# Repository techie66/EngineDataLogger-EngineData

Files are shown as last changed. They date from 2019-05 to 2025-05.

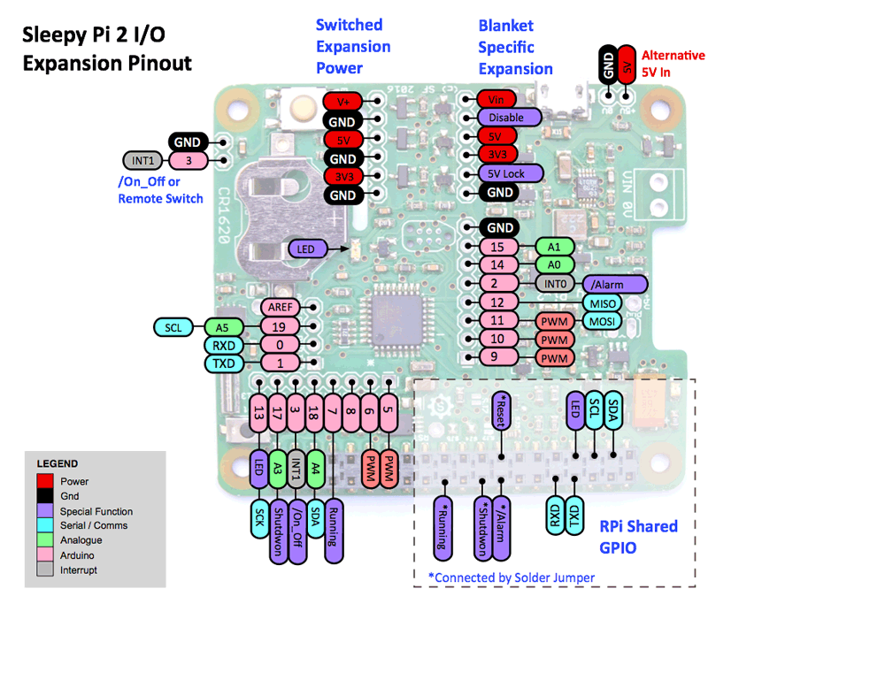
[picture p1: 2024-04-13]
hardware/Sleepy-Pi-2-Expansion-Annotated-2-1000.png

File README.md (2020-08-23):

# Engine Data Logger - Engine Data
This project has been developed using Automake and Makefile setup from: https://github.com/sudar/Arduino-Makefile

Sleepy Pi 2 needs to have software power jumper enabled if programming from the Pi.
	i2cset -y 1 0x24 0xFD
Turn it off with:
	i2cset -y 1 0x24 0xFF

It's not strictly necessary, but Arduino-Makefile includes a script to reset the Arduino. It would need to be setup to set pin 22 of the RPi's GPIO high for about 1/3 of a second. Alternatively, https://github.com/SpellFoundry/avrdude-rpi provides a patched avrdude that handles this for you. This is the approach I have setup here. The Makefile points to a special avr_tools directory that contains this patched version. None of this is necessary if you are willing to manually hit the reset button whenever you try to upload code.

## Componenents
- [EngineDataLogger(EDL)](https://github.com/techie66/EngineDataLogger)
- [EDL - Dashboard](https://github.com/techie66/EngineDataLogger---Dashboard)
- [EDL - Front Controls](https://github.com/techie66/EngineDataLogger-FrontControls)
- ->[EDL - EngineData](https://github.com/techie66/EngineDataLogger-EngineData)

# License
EngineDataLogger is licensed under the GNU GPLv2. Dependencies are licensed under their respective licenses. See LICENSE for full text of GPLv2.

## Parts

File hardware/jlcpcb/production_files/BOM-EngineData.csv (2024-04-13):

Comment | Designator | Footprint | LCSC
15V standoff | D1,D4 | D_SMB | C113989
1k | R23,R24,R6,R7,R9 | R_0402_1005Metric | C11702
100nf | C1,C13,C14,C2,C3,C4,Cboot1 | C_0402_1005Metric | C1525
MCP2515-xSO | U12,U5 | SOIC-18W_7.5x11.6mm_P1.27mm | C153782
33pf | C15,C16,C5,C6 | C_0402_1005Metric | C1562
TCA9517DR | U8 | SOIC-8_L4.9-W3.9-P1.27-LS6.0-BL | C182421
EL817 | U2,U9 | EasyEDA-C183799-smd-SOP-4_L6.5-W4.6-P2.54-LS10.2-TL | C183799
120R | R11,R16 | R_0402_1005Metric | C25079
470 | R5 | R_0402_1005Metric | C25117
100k | R12,R13,R17,R18,Rfbt1 | R_0402_1005Metric | C25741
10k | R10,R8 | R_0603_1608Metric | C25804
24K9 1% | Rfbb1 | R_0402_1005Metric | C25874
1 uF | C9 | C_0805_2012Metric | C28323
8uH, 14m | L1 | L_Bourns_SRP7028A_7.3x6.6mm | C408450
2k | R19,R2,R20,R3,R4 | R_0402_1005Metric | C4109
2.2k | R1 | R_0603_1608Metric | C4190
10uf | Cin1 | C_0805_2012Metric | C440198
22uF | Cout1,Cout2,Cout3,Cout4 | C_0805_2012Metric | C45783
30pf | C17,C18 | C_0402_1005Metric | C5182450
220nf | Chf1 | C_0805_2012Metric | C5378
14.7456 Mhz | Y3 | Crystal_SMD_3225-4Pin_3.2x2.5mm | C557186
SC16IS752IPW | U14 | TSSOP-28_4.4x9.7mm_P0.65mm | C57156
TXB0104PW | U13,U3 | TSSOP-14_4.4x5mm_P0.65mm | C60708
TJA1051T | U11,U4 | SOIC-8_3.9x4.9mm_P1.27mm | C6952
LMR33630ADDA | U7 | Texas_HSOP-8-1EP_3.9x4.9mm_P1.27mm_ThermalVias | C841384
12Mhz | Y1,Y2 | Crystal_SMD_3225-4Pin_3.2x2.5mm | C9002
Jumper_NO_Small | JP1 | SolderJumper-2_P1.3mm_Open_RoundedPad1.0x1.5mm
Jumper_NO_Small | JP2 | SolderJumper-2_P1.3mm_Open_RoundedPad1.0x1.5mm

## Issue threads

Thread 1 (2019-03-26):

"programming mode"

techie66, 2019-03-26:
enable a "programming mode" that lets a controlling I2C master set conversion factors.
-Store them in flash
-I2C read/write
-Separate values for each variable in conversion factor (wheel diameter, pulses per rotation, etc...)

techie66, 2020-02-27:
eb993df9de465faafcb15cc0d58ad687136bdcc4 added the functions that enable this. Just have to define an interface to actually do it.

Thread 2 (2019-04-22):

Odometer

techie66, 2019-04-22:
Project needs an odometer.
1. Basic setting should be tire diameter
2. EEPROM storage
3. Only write to eeprom on power off.
4. Rotate storage area.

techie66, 2019-04-22:
#1 Programming mode should enable setting diameter

techie66, 2019-04-23:
I've got a local commit that does 1 and 2 from above.  EEPROM is read during setup and globals are set and updated via the wheel ISR.
Just need to handle writing data back to EEPROM which should take care of 3 and 4.

techie66, 2020-02-27:
This is all taken care of by eb993df9de465faafcb15cc0d58ad687136bdcc4

Closed 2020-02-27.

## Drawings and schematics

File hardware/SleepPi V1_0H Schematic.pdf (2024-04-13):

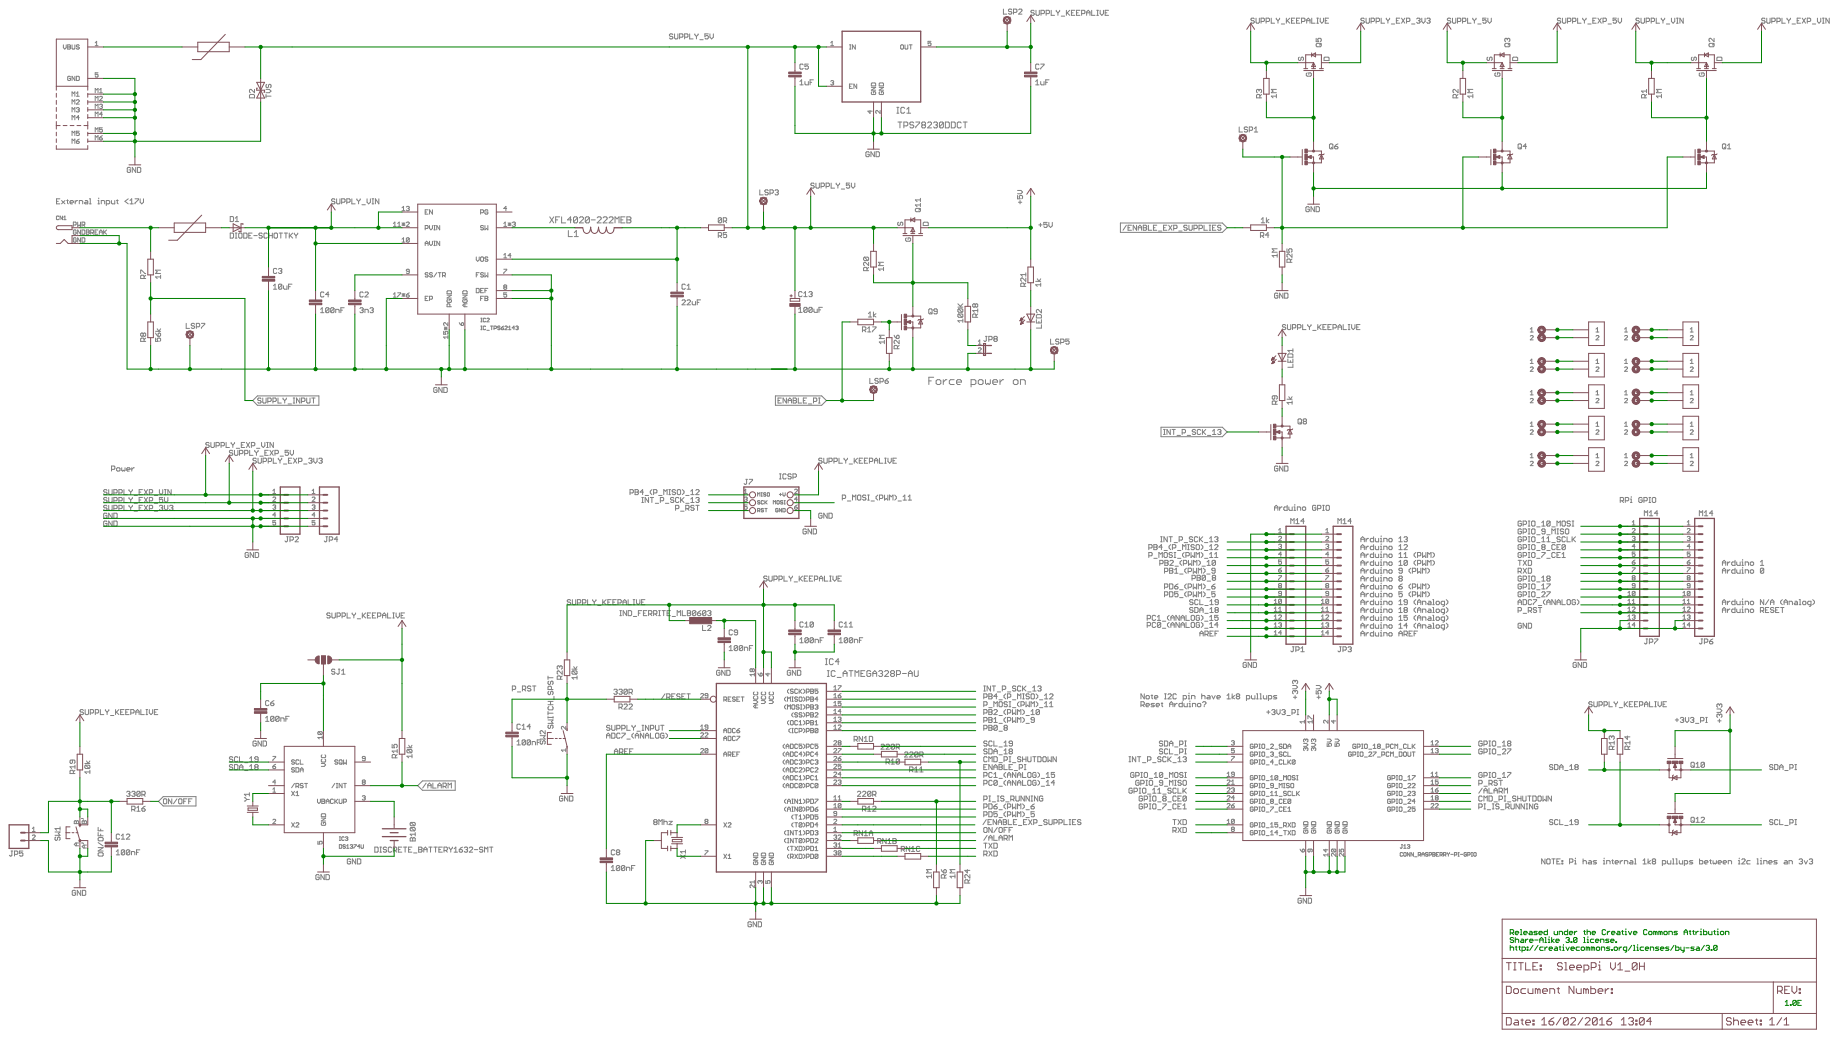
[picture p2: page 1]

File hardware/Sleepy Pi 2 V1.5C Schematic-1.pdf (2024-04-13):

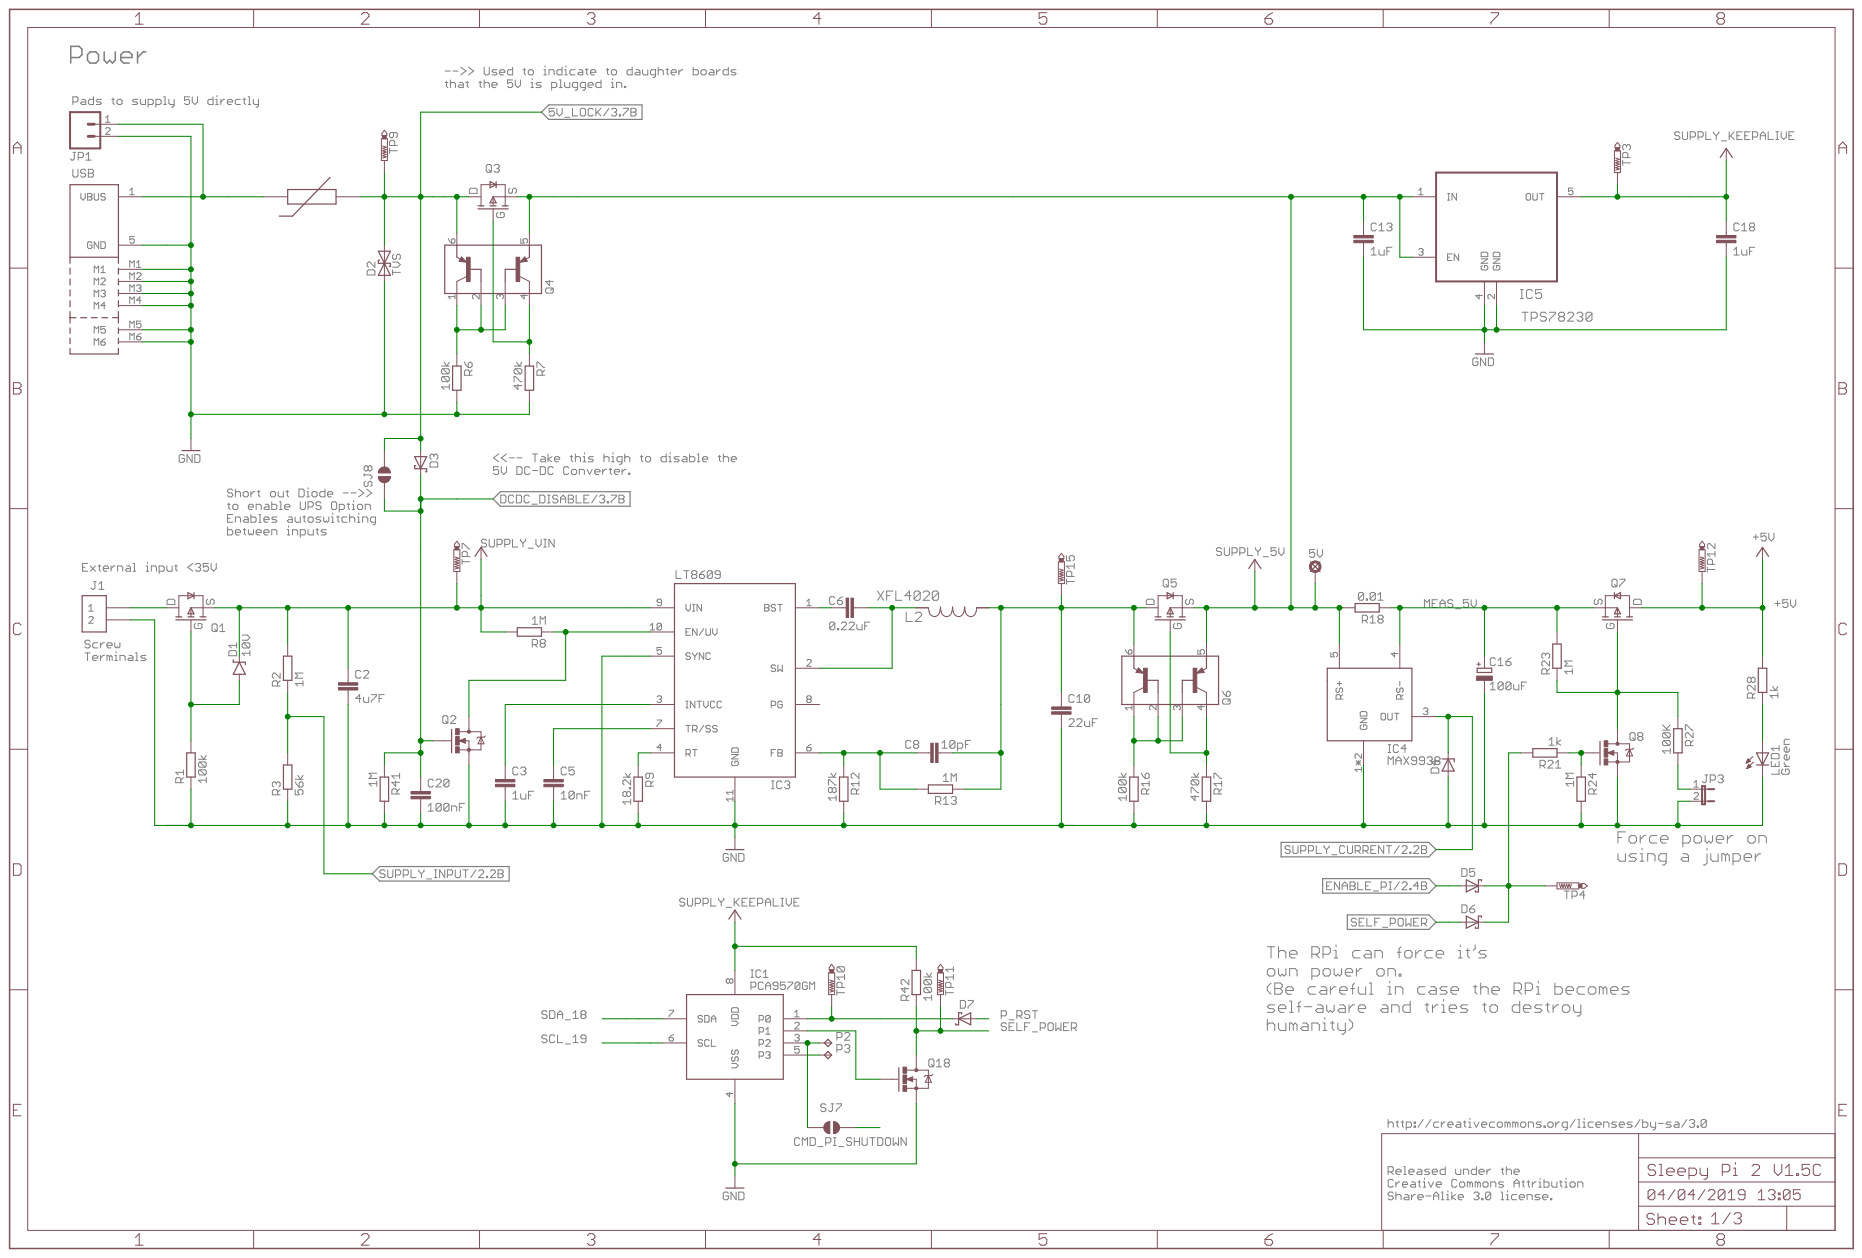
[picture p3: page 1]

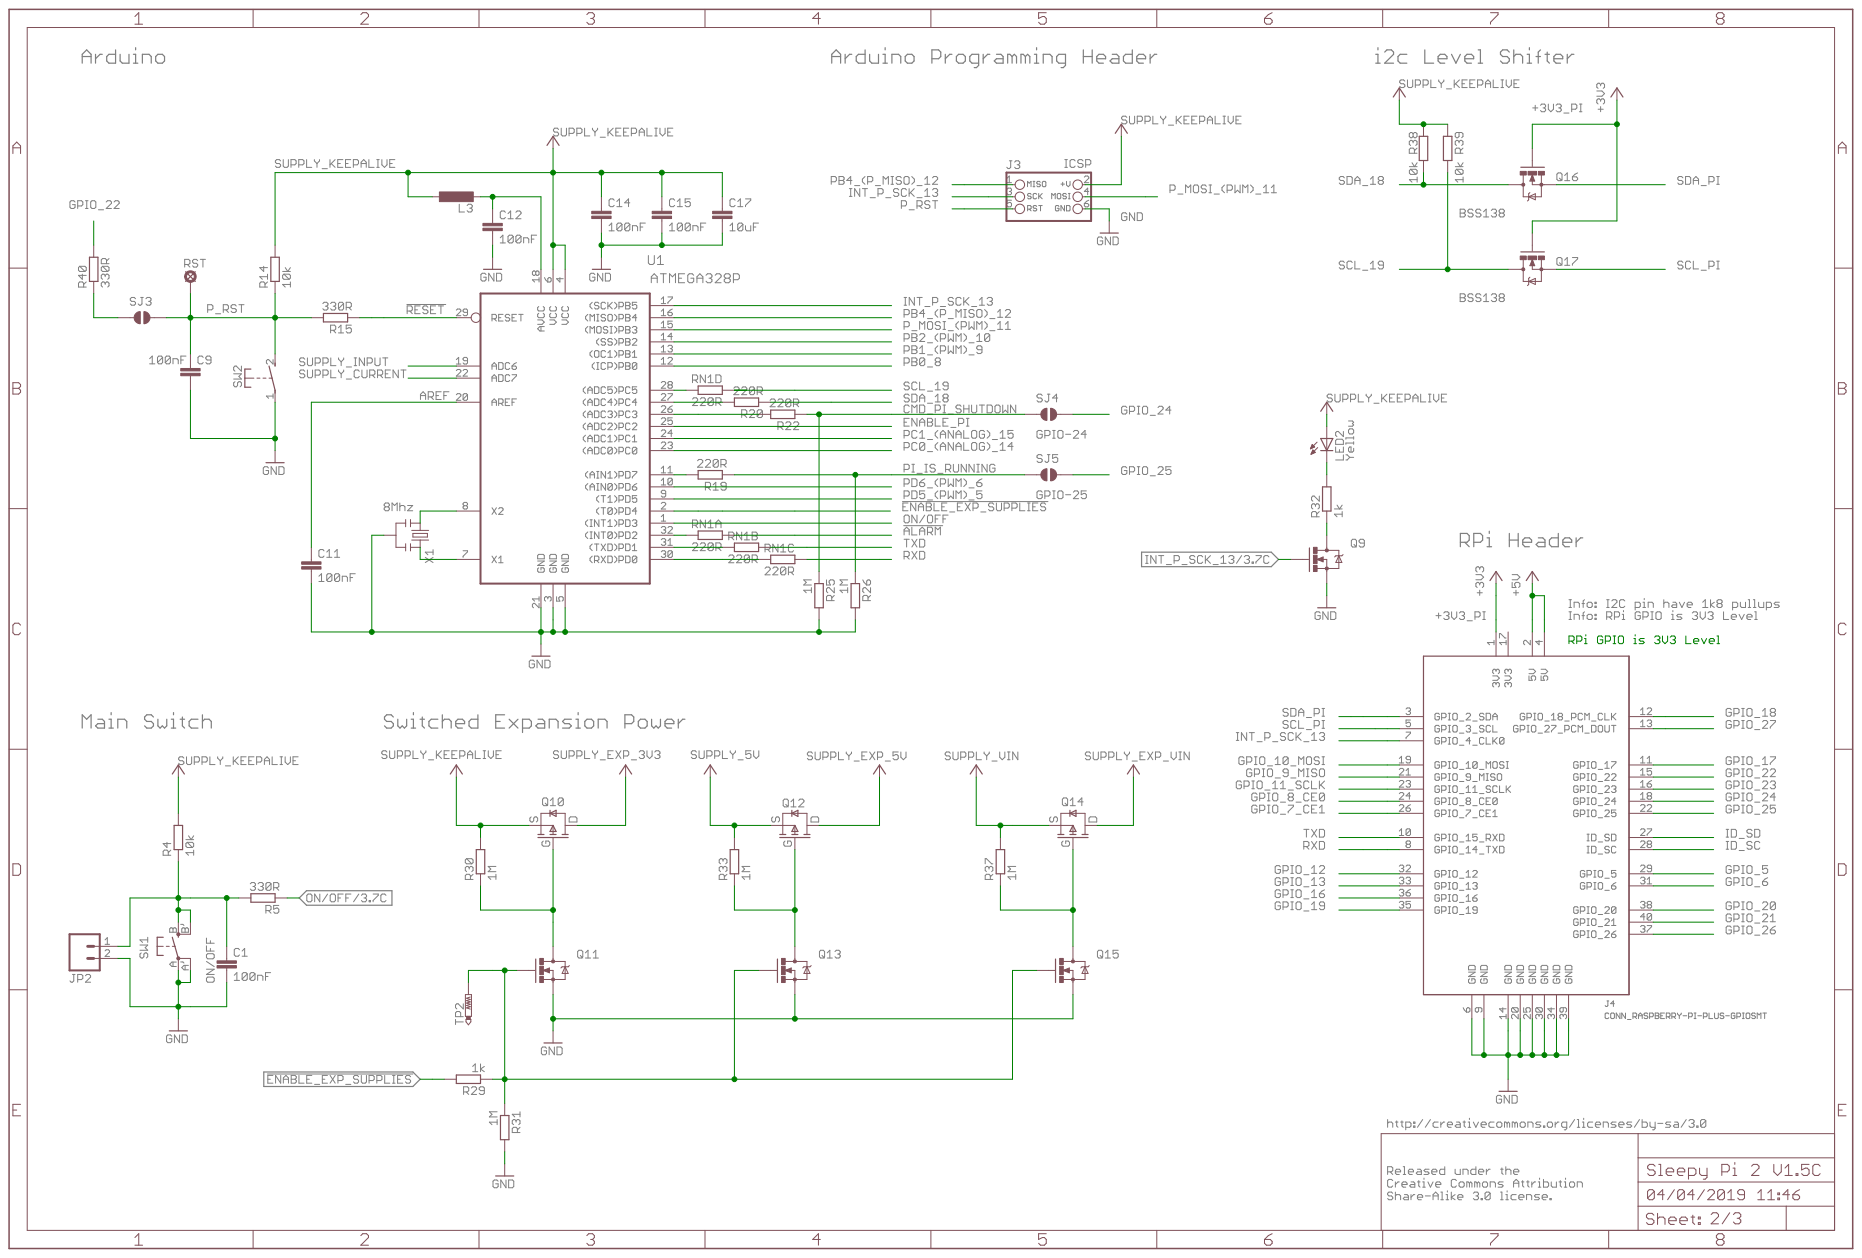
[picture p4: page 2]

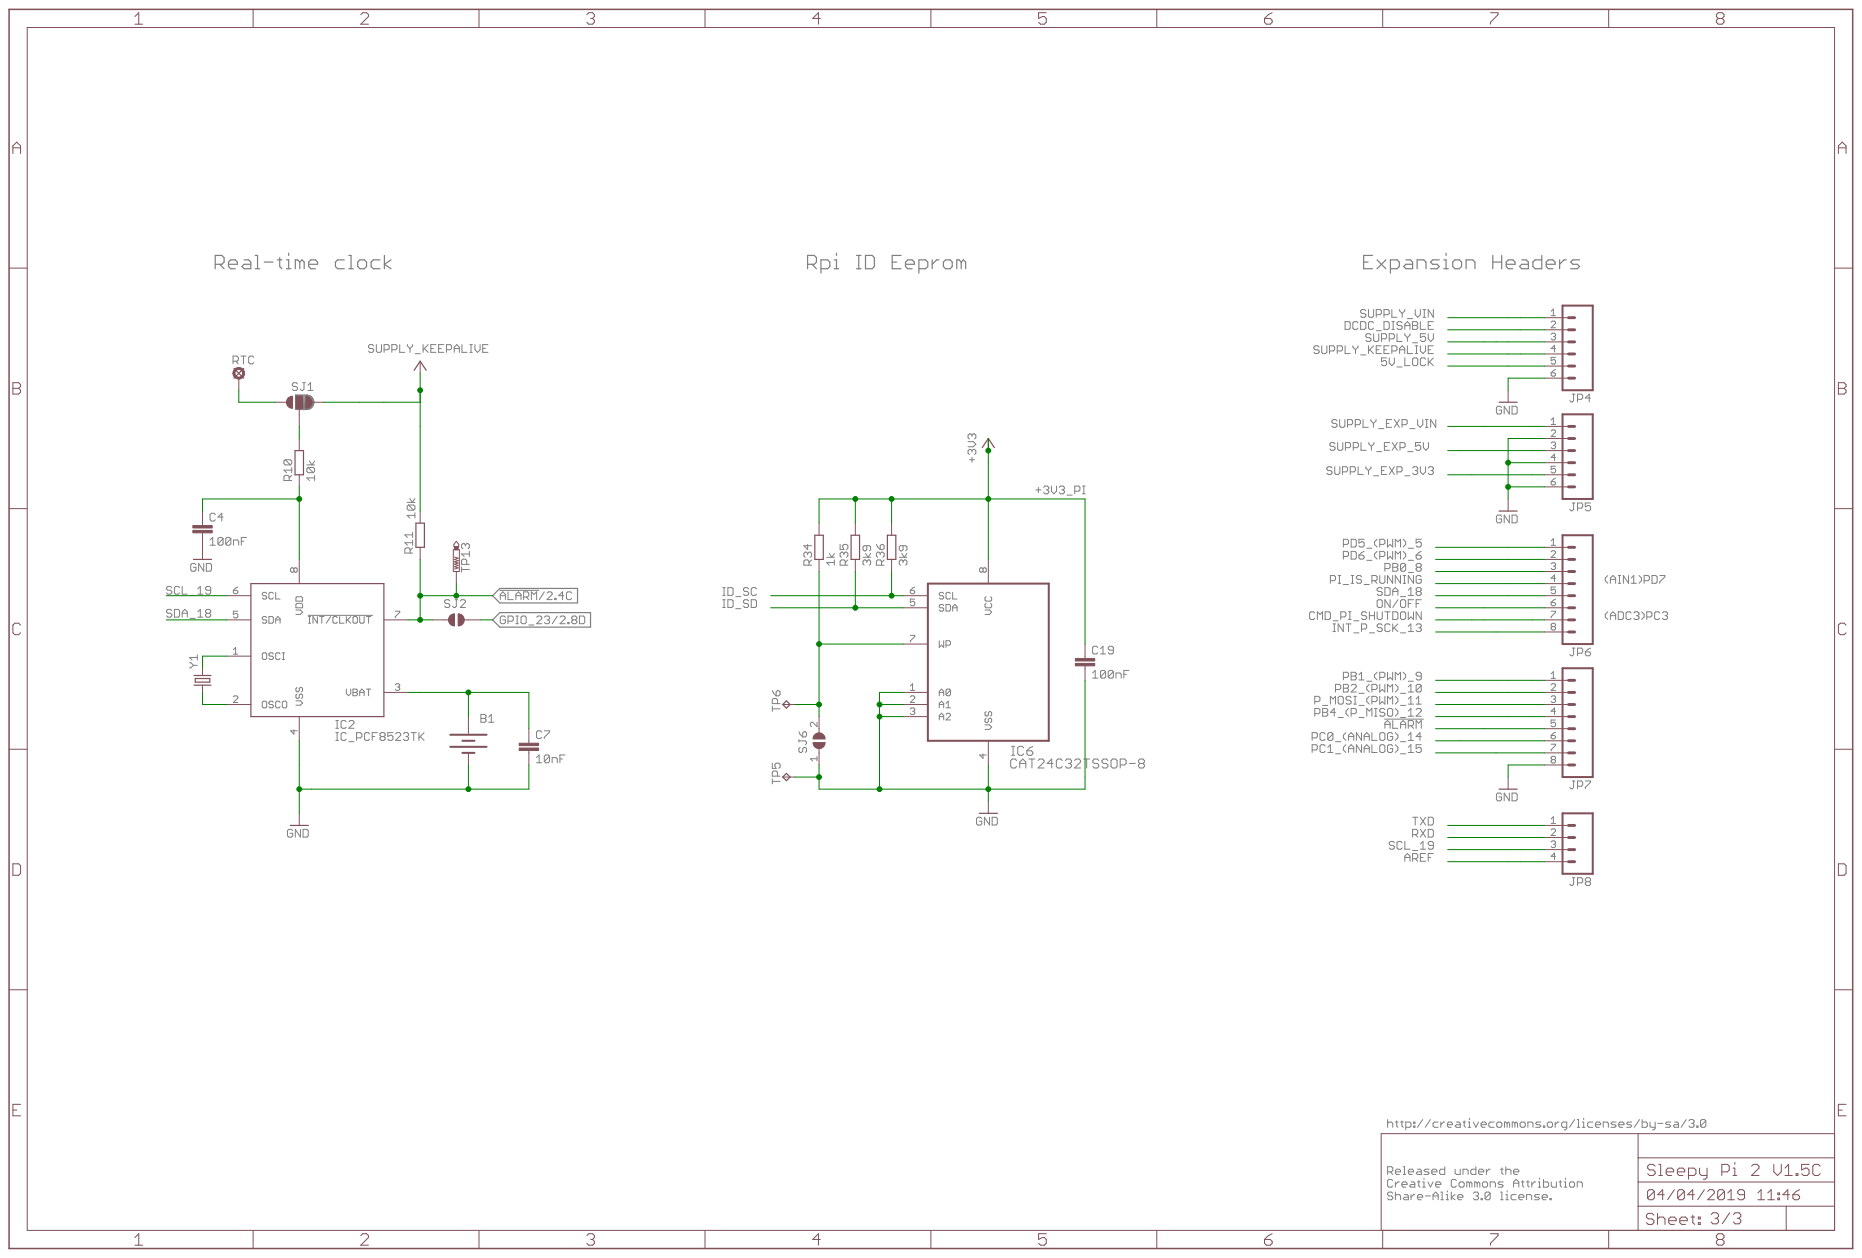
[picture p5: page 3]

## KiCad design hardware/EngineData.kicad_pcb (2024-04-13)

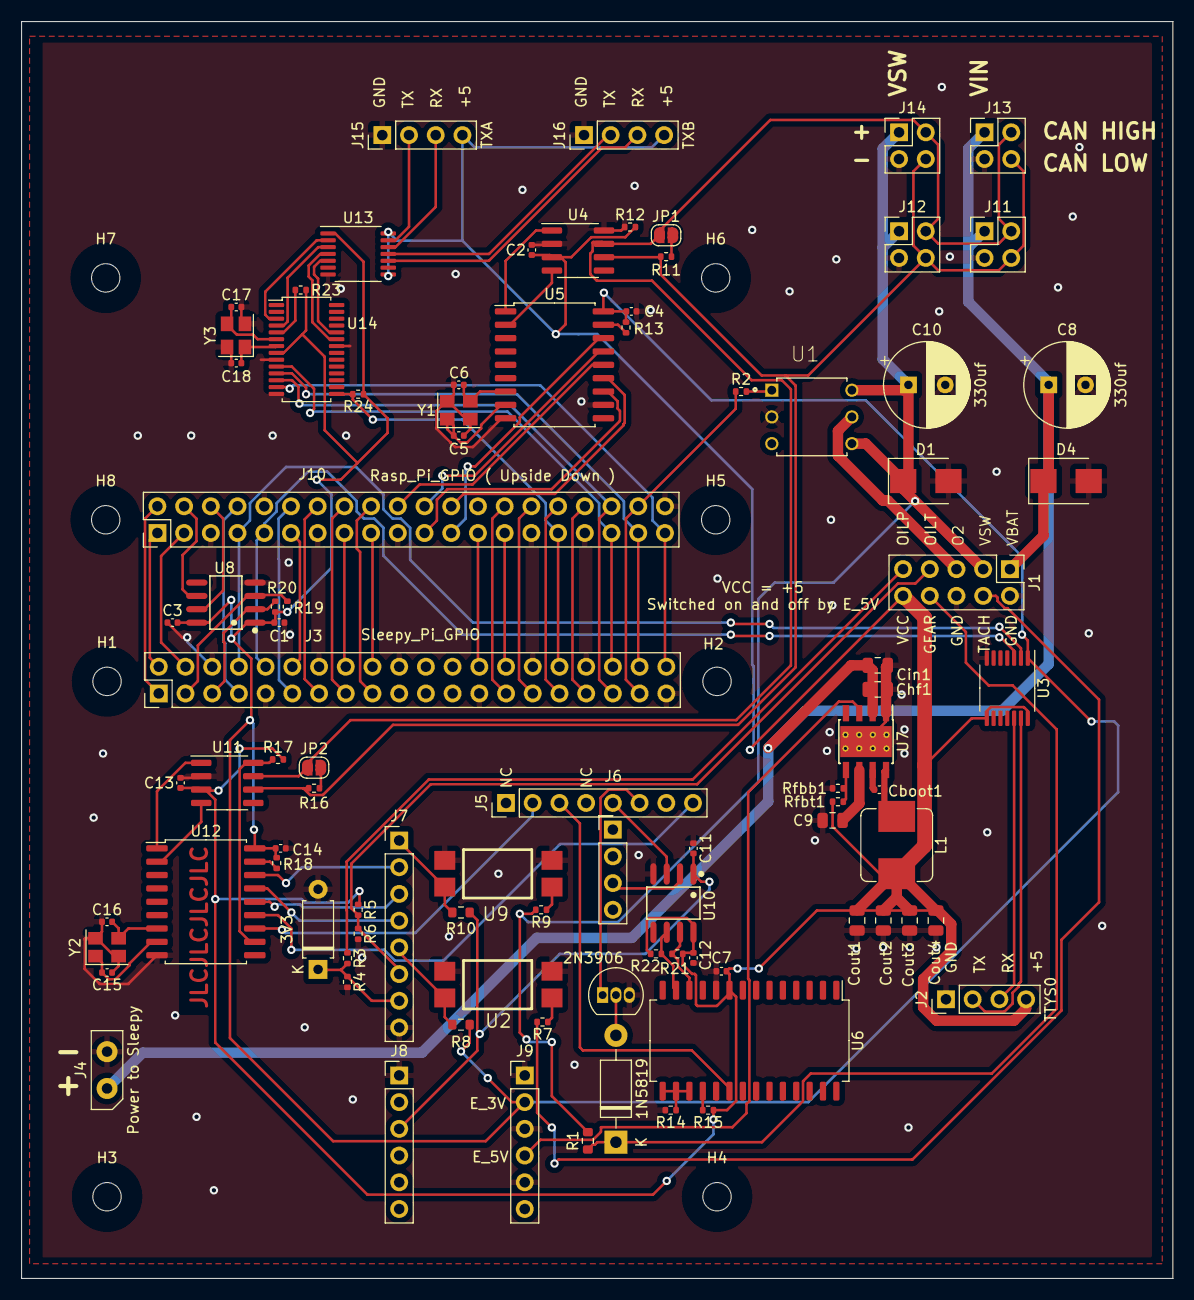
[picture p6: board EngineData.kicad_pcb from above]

Board: 2 copper layers, 109.5 x 119.5 mm, 100 parts (0 on the bottom side), 98 nets.

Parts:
C1, C2, C3, C4, C7, C11, C12, C13, C14: 100nf; C_0402_1005Metric
C5, C6, C15, C16: 33pf; C_0402_1005Metric
C8, C10: 330uf; CP_Radial_D8.0mm_P3.50mm
C9: 1 uF; C_0805_2012Metric
C17, C18: 30pf; C_0402_1005Metric
Cboot1: 100nf; C_0402_1005Metric
Chf1: 220nf; C_0805_2012Metric
Cin1: 10uf; C_0805_2012Metric
Cout1, Cout2, Cout3, Cout4: 22uF; C_0805_2012Metric
D1, D4: 15V standoff; D_SMB
D2: 1N5819; D_DO-41_SOD81_P10.16mm_Horizontal
D3: 3V3; D_A-405_P7.62mm_Horizontal
H1, H2, H3, H4, H5, H6, H7, H8: MountingHole; MountingHole_2.7mm_M2.5
J1: External Connector; PinHeader_2x05_P2.54mm_Vertical
J2: TTYS0; PinHeader_1x04_P2.54mm_Vertical
J3: Sleepy_Pi_GPIO; PinHeader_2x20_P2.54mm_Vertical
J4: Power to Sleepy; S_Pi_PWR
J5, J7: Conn_01x08; PinHeader_1x08_P2.54mm_Vertical
J6: Conn_01x04; PinHeader_1x04_P2.54mm_Vertical
J8, J9: Conn_01x06; PinHeader_1x06_P2.54mm_Vertical
J10: Rasp_Pi_GPIO ( Upside Down ); PinHeader_2x20_P2.54mm_Vertical
J11, J12, J13, J14: 2x2; PinHeader_2x02_P2.54mm_Vertical
J15: TXA; PinHeader_1x04_P2.54mm_Vertical
J16: TXB; PinHeader_1x04_P2.54mm_Vertical
JP1, JP2: Jumper_NO_Small; SolderJumper-2_P1.3mm_Open_RoundedPad1.0x1.5mm
L1: 8uH, 14m; L_Bourns_SRP7028A_7.3x6.6mm
Q1: 2N3906; TO-92_Inline
R1: 2.2k; R_0603_1608Metric
R2, R3, R4, R19, R20: 2k; R_0402_1005Metric
R5: 470; R_0402_1005Metric
R6, R7, R9, R23, R24: 1k; R_0402_1005Metric
R8, R10: 10k; R_0603_1608Metric
R11, R16: 120R; R_0402_1005Metric
R12, R13, R15, R17, R18: 100k; R_0402_1005Metric
R14, R21, R22: 4K7 1%; R_0402_1005Metric
Rfbb1: 24K9 1%; R_0402_1005Metric
Rfbt1: 100k 1%; R_0402_1005Metric
U1: G3VM-31BR; DIP762W50P254L737H485Q6
U2, U9: EL817; EasyEDA-C183799-smd-SOP-4_L6.5-W4.6-P2.54-LS10.2-TL
U3, U13: TXB0104PW; TSSOP-14_4.4x5mm_P0.65mm
U4, U11: TJA1051T; SOIC-8_3.9x4.9mm_P1.27mm
U5, U12: MCP2515-xSO; SOIC-18W_7.5x11.6mm_P1.27mm
U6: MCP23017-E/SO; SOIC-28W_7.5x18.7mm_P1.27mm
U7: LMR33630ADDA; Texas_HSOP-8-1EP_3.9x4.9mm_P1.27mm_ThermalVias
U8, U10: TCA9517DR; SOIC-8_L4.9-W3.9-P1.27-LS6.0-BL
U14: SC16IS752IPW; TSSOP-28_4.4x9.7mm_P0.65mm
Y1, Y2: 12Mhz; Crystal_SMD_3225-4Pin_3.2x2.5mm
Y3: 14.7456 Mhz; Crystal_SMD_3225-4Pin_3.2x2.5mm

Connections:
3V3: C11.2, J8.3, R10.2, U10.1 (VCCA)
/CAN_H: J11.2, J12.2, J13.2, J14.2, JP1.1 (A), JP2.1 (A), U4.7 (CANH), U11.7 (CANH)
/CAN_L: J11.4, J12.4, J13.4, J14.4, R11.1, R16.1, U4.6 (CANL), U11.6 (CANL)
/GE1: J3.2, J10.1
/GE2: J3.4, J10.3
/GE4: J3.8, J10.7, U3.2 (A1)
/GE5: J3.10, J10.9, U3.3 (A2)
/GE6: J3.12, J10.11
/GE8: J3.16, J10.15
/GE9: J3.18, J10.17
/GE11: J10.21, U5.12 (~INT)
/GE12: J10.23, U5.16 (~CS)
/GE13: J3.26, J10.25
/GE14: J3.28, J10.27
/GE16: J3.32, J10.31, R24.2, U14.15 (~IRQ)
/GE18: J3.36, J10.35, U14.10 (A0/~CS)
/GE19: J3.38, J10.37, U14.11 (A1/SI)
/GE20: J3.40, J10.39, U14.13 (SCL/SCLK)
/GEAR: D2.1 (K), J1.8, R1.1
/GO1: J3.1, J10.2
/GO4: J3.7, J10.8
/GO6: J3.11, J10.12
/GO7: J3.13, J10.14
/GO8: J3.15, J10.16
/GO9: J3.17, J10.18
/GO10: J10.20, U5.14 (SI)
/GO11: J10.22, U5.15 (SO)
/GO12: J10.24, U5.13 (SCK)
/GO14: J3.27, J10.28
/GO15: J3.29, J10.30
/GO16: J3.31, J10.32
/GO17: J3.33, J10.34
/GO18: J3.35, J10.36, U14.12 (n.c./SO)
/GO19: J3.37, J10.38, R2.1
/IO Expander/SCL: R21.1, U6.12 (SCK), U10.7 (SCLB)
/IO Expander/SDA: R22.1, U6.13 (SDA), U10.6 (SDAB)
/MCP2515 w|trans1/EN_TX: R17.1, U11.8 (S), U12.11 (~RX0BF)
/MCP2515 w|trans1/RXCAN: U11.4 (RXD), U12.2 (RXCAN)
/MCP2515 w|trans1/TXCAN: U11.1 (TXD), U12.1 (TXCAN)
/MCP2515 w|trans/RXCAN: U4.4 (RXD), U5.2 (RXCAN)
/MCP2515 w|trans/TXCAN: U4.1 (TXD), U5.1 (TXCAN)
/O2POW: J1.5, U1.5
/OIL_P: J1.9, R3.1
/OIL_T: J1.7, J7.6, R5.2, R6.1
/PB0_8: J5.3, U6.20 (INTA)
/PB1_9: J7.1, R10.1, U9.4
/PB2_10: J7.2, U12.16 (~CS)
/PC1_A1: D3.1 (K), J7.7, R3.2, R4.1
/PD2_2: J7.5, R8.1, U2.4
/PD3_3: J5.6, Q1.1 (E)
/PD6_6: J5.2, U12.12 (~INT)
/PI_SCL: J10.6, U8.7 (SCLB)
/Pi_SDA: J10.4, U8.6 (SDAB)
/SH_SCL: J3.5, R20.2, U8.2 (SCLA)
/SH_SDA: J3.3, R19.2, U8.3 (SDAA)
/S_MISO_12: J7.4, U12.15 (SO)
/S_MOSI_11: J7.3, U12.14 (SI)
/S_SCK: J5.8, U12.13 (SCK)
/S_SCL: J6.3, U10.2 (SCLA)
/S_SDA: J5.5, U10.3 (SDAA)
/TACH: J1.4, R7.2
/UARTs/RST: R23.2, U14.5 (~RESET)
/UARTs/RXA: U13.3 (A2), U14.4 (RXA)
/UARTs/RXB: U13.5 (A4), U14.24 (RXB)
/UARTs/TXA: U13.2 (A1), U14.3 (TXA)
/UARTs/TXB: U13.4 (A3), U14.23 (TXB)
/VBAT: C8.1, Chf1.2, Cin1.2, D4.1 (A1), J1.1, J4.1, J11.1, J13.1, U7.2 (VIN)
/VSW: C10.1, D1.1 (A1), J1.3, J12.1, J14.1, R1.2, R9.2, U1.4, U1.6
E_3V3: C1.2, C3.2, C4.2, C14.2, J9.2, R8.2, R13.2, R18.2, R19.1, R20.1, R23.1, R24.1, U3.1 (VCCA), U5.18 (VDD), U8.1 (VCCA), U8.8 (VCCB), U12.18 (VDD), U13.1 (VCCA), U14.8 (VDD)
E_5V: J9.4, U7.3 (EN)
GND: C1.1, C2.2, C3.1, C4.1, C5.1, C6.1, C7.2, C8.2, C9.1, C10.2, C11.1, C12.1, C13.2, C14.1, C15.1, C16.1, C17.2, C18.1, Chf1.1, Cin1.1, Cout1.2, Cout2.2, Cout3.2, Cout4.2, D1.2 (A2), D3.2 (A), D4.2 (A2), J1.2, J1.6, J2.1, J3.6, J3.9, J3.14, J3.20, J3.25, J3.30, J3.34, J3.39, J4.2, J7.8, J8.1, J9.1, J9.3, J9.5, J10.5, J10.10, J10.13, J10.19, J10.26, J10.29, J10.33, J10.40, J11.3, J12.3, J13.3, J14.3, J15.1, J16.1, Q1.3 (C), R4.2, R6.2, R12.1, R14.2, Rfbb1.2, U1.2, U2.2, U2.3, U3.7 (GND), U4.2 (GND), U4.8 (S), U5.9 (VSS), U5.11 (~RX0BF), U6.10 (VSS), U7.1 (PGND), U7.9 (AGND), U8.4 (GND), U9.2, U9.3, U10.4 (GND), U11.2 (GND), U12.9 (VSS), U13.7 (GND), U14.9 (I2C/~SPI), U14.14 (SDA/VSS), U14.22 (VSS), Y1.2, Y1.4, Y2.2, Y2.4, Y3.2, Y3.4
unnamed: C5.2, U5.8 (OSC1), Y1.1
unnamed: C6.2, U5.7 (OSC2), Y1.3
unnamed: C9.2, U7.6 (VCC)
unnamed: C15.2, U12.8 (OSC1), Y2.1
unnamed: C16.2, U12.7 (OSC2), Y2.3
unnamed: C17.1, U14.6 (XTAL1), Y3.3
unnamed: C18.2, U14.7 (XTAL2), Y3.1
unnamed: Cboot1.1, U7.7 (BOOT)
unnamed: Cboot1.2, L1.1, U7.8 (SW)
unnamed: D2.2 (A), Q1.2 (B)
unnamed: J2.2, U3.13 (B1)
unnamed: J2.3, U3.12 (B2)
unnamed: J15.2, U13.13 (B1)
unnamed: J15.3, U13.12 (B2)
unnamed: J16.2, U13.11 (B3)
unnamed: J16.3, U13.10 (B4)
unnamed: JP1.2 (B), R11.2
unnamed: JP2.2 (B), R16.2
unnamed: R2.2, U1.1
unnamed: R7.1, U2.1
unnamed: R9.1, U9.1
unnamed: R13.1, U5.17 (~RESET)
unnamed: R14.1, U6.15 (A0), U6.16 (A1), U6.17 (A2)
unnamed: R15.2, U6.18 (~RESET)
unnamed: R18.1, U12.17 (~RESET)
unnamed: Rfbb1.1, Rfbt1.1, U7.5 (FB)
VCC: C2.1, C7.1, C12.2, C13.1, Cout1.1, Cout2.1, Cout3.1, Cout4.1, J1.10, J2.4, J15.4, J16.4, L1.2, R5.1, R12.2, R15.1, R17.2, R21.2, R22.2, Rfbt1.2, U3.8 (OE), U3.14 (VCCB), U4.3 (VCC), U6.9 (VDD), U10.8 (VCCB), U11.3 (VCC), U13.8 (OE), U13.14 (VCCB)

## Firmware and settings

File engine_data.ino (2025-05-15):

#include <SleepyPi2.h>
#include <Time.h>
#include <LowPower.h>
#include <PCF8523.h>
#include <Wire.h>
#include <PinChangeInterrupt.h>
#include <EEPROM.h>
#include "EDL_eeprom.h"
#include <mcp2515_can.h>

#define     SLAVE_ADDRESS 0x04
// CAN Constants
#define SPI_CS_PIN 10
mcp2515_can CAN(SPI_CS_PIN); // Set CS pin


#define     MAX_UINT16_T 4294967295
#define     INCHES_PER_MILE 63360
#define     MICROS_SECOND 1000000
#define     MICROSECONDS_MINUTE MICROS_SECOND * 60
#define     MICROSECONDS_HOUR MICROSECONDS_MINUTE * 60
#define     EEPROM_WRITE_LIMT 50000
#define     EEPROM_SIZE 1024
#define     EEPROM_CONFIG_BUFFER 128
#define     CANID_RESET_TRIP 0x230
#define     CANID_ENGINE1 0x227
#define     CANID_ENGINE2 0x228
#define     CAN_ENGINE1_RATE 200
#define     CAN_ENGINE2_RATE 5000

const int   bikeOnPin = 9,
            rpmPulsePin = 2,
            wheelPulsePin = 3,
            oil_Temp_pin = A0,
            oil_pres_pin = A1;

const uint8_t   rpm_pulses = 10,  // How many pulses to average
                speed_pulses = 200;

volatile uint32_t running_odometer,
         running_trip,
         pulses_per_hundredth_mile,
         odometer_pulses = 0;
volatile bool ready_to_save_odo = false;
const int odo_save_interval_hundredths = 100;
float inches_per_pulse;
unsigned long SHUTDOWN_DELAY = 60000;
uint32_t MPH_CONV;
uint32_t RPM_CONV;

uint16_t rpm = 0,
         temp_oil = 0, // hundredths, F
         speed = 0,
         pres_oil = 0; // hundredths, psi
float supply_voltage = 0.0;
volatile unsigned long  RPM_interval = 0,
                        SPEED_interval = 0,
                        rpm_time_last = 0,
                        speed_time_last = 0,
                        rpm_wkg_micros = 0,
                        speed_wkg_micros = 0;
volatile unsigned long  rpm_pulse_times[rpm_pulses] = {0},
    speed_pulse_times[speed_pulses] = {0};
volatile bool bike_running = false;
unsigned long wkgTime = 0,
              time,
              time_BikeOff = 0;

volatile uint8_t rpm_pulse_count = 0,
                 speed_pulse_count = 0;;

boolean debug = false;

// ISR to get pulse interval for RPM(engine)
// a little longer than I'd like, since it handles the averaging
// but it saves clock cycles overall by only calculating interval once
void rpmPulse()
{
  // Save current micros
  rpm_wkg_micros = micros();
  // increment counter and reset if necessary
  rpm_pulse_count++;
  if (rpm_pulse_count >= rpm_pulses) {
    rpm_pulse_count = 0;
  }
  // decrement RPM_interval by oldest interval
  RPM_interval -= rpm_pulse_times[rpm_pulse_count];
  // save new interval and add to RPM_interval
  rpm_pulse_times[rpm_pulse_count] = (rpm_wkg_micros - rpm_time_last);
  RPM_interval += rpm_pulse_times[rpm_pulse_count];
  // Save last time we were called
  rpm_time_last = rpm_wkg_micros;
}


// ISR to get pulse interval for wheel(engine)
// same documentation as rpmPulse
void wheelPulse()
{
  speed_wkg_micros = micros();
  speed_pulse_count++;
  odometer_pulses++;
  if (speed_pulse_count >= speed_pulses) {
    speed_pulse_count = 0;

    /*// non-running average
    SPEED_interval = speed_wkg_micros - speed_time_last;
    speed_time_last = speed_wkg_micros;
    */
  }
  if (odometer_pulses > pulses_per_hundredth_mile) {
    static int running_ticks_to_save = 0;
    odometer_pulses = 0;
    running_odometer++;
    running_ticks_to_save++;
    if ( running_ticks_to_save >= odo_save_interval_hundredths ) {
      ready_to_save_odo = true;
      running_ticks_to_save = 0;
    }
  }

  SPEED_interval -= speed_pulse_times[speed_pulse_count];
  speed_pulse_times[speed_pulse_count] = (speed_wkg_micros - speed_time_last);
  SPEED_interval += speed_pulse_times[speed_pulse_count];
  speed_time_last = speed_wkg_micros;

}

// ISR to signal bike is on
void bikeOn()
{
  bike_running = !digitalRead(bikeOnPin);
}

// Output serial debug if debug is true
void debug_out(const char str[])
{
  if (debug) {
    Serial.write(str, strlen(str));
  }
}

double Thermistor(int RawADC)
{
  /*Calculates temperature from analog reading
   * Schematic :
   * +Vs---R1---+---+---R3--GND
   *            |   |
   *           ADC  +--Rth--GND
   *
   * R1 and R3 chosen to provide no more that Vref at ADC
   * when Thermistor is disconnected (ie Rth=infinity)
   * and acceptable current when thermistor is shorted (ie Rth=0)
   */
  double Temp;
  double Rth; // Thermistor Resistance
  double Vo;
  double R2;
  // Easiest way to calibrate is to adjust the resistor values slightly
  static const double R1 = 460.0; // +side resistor
  static const double R3 = 1000.0; // -side resistor
  static const double Rconn = 0.0; // sensor connection resistance
  static const double Vs = 5.06; // voltage connected to +side resistor
  static const double Vref = 3.26; // analog reference voltage
  static const double SHA = .001600646526;
  static const double SHB = .0002607956449;
  static const double SHC = -0.00000004456663162;

  /*calculations*/
  Vo = (RawADC / 1024.0) * Vref;
  R2 = (Vo * R1) / (Vs - Vo);
  Rth = (R3 * R2) / (R3 - R2) - Rconn;
  Temp = log(Rth); //Temporarily holds the value of log(Rth) to be used below

  // Steinhart-Hart (factored to reduce calculations a bit)
  Temp = 1 / (SHA + (SHB + (SHC * Temp * Temp )) * Temp );
  Temp = Temp - 273.15;            // Convert Kelvin to Celcius
  Temp = (Temp * 9.0) / 5.0 + 32.0; // Convert Celcius to Fahrenheit
  return Temp;
}

double oilPressure( int RawADC ) {
	/* oilPressure
	   * Calculate oil pressure from ADC reading
	   *
	   *
	*/
	static const double Vref = 3.26;
	// Generic conversion factor from V to pressure unit, assumed linear
  /*  Ambient = 14.7 psi = 0.5V from transducer = 0.25V after voltage divider
   *  Max = 150 psi = 4.5V from transducer = 2.25V after voltage divider
   *  Calculate slope of regression line and that is Vconv
  */
	static const double Vconv = 75.0; // Max = 150
  static const double pfac = 0; // linear correction
  //static const double pfac = 18.75; // linear correction
	//static const double Vconv = 792.6; // Max = 1600
  //static const double pfac = 175; // linear correction
  double intermediate = (((RawADC/1024.0) * Vref)) * Vconv;
  if ( intermediate > pfac ) return intermediate - pfac; 
  else return 0;
}

/*
 * Basic linear compensation for presure reading
 * not very accurate
 */
uint16_t compensateOilPressure(uint16_t p, uint16_t t)
{
  uint16_t compensatedPressure=p;
  double compensationFactor = 0.037222;
  if ( t > 7000) {
    compensatedPressure = p + ((t - 7000) * compensationFactor);
  }
  return compensatedPressure;
}

void readEEPROM()
{
  int eeAddress = 0;
  config eeprom_config;

  EEPROM.get(eeAddress, eeprom_config);
  odometer saved_odometer;

  EEPROM.get(eeprom_config.odo_address, saved_odometer);
  running_odometer = saved_odometer.miles_hundredths;
  running_trip = saved_odometer.trip_hundredths;

  inches_per_pulse = (eeprom_config.rear_diameter / 100.0 * PI) / eeprom_config.rear_teeth;
  pulses_per_hundredth_mile = (INCHES_PER_MILE / 100) / inches_per_pulse;

  SHUTDOWN_DELAY = eeprom_config.shutdown_delay;
  MPH_CONV = 100 * inches_per_pulse * MICROSECONDS_HOUR * speed_pulses / INCHES_PER_MILE;
  RPM_CONV = MICROSECONDS_MINUTE * rpm_pulses;
}

void saveOdometer()
{
  int eeAddress = 0;
  config eeConfig;
  EEPROM.get(eeAddress, eeConfig);

  odometer eeOdometer;
  EEPROM.get(eeConfig.odo_address, eeOdometer);
  if ((running_odometer > eeOdometer.miles_hundredths) || (running_trip > eeOdometer.trip_hundredths)) {
    //Update EEPROM Odometer
    eeOdometer.miles_hundredths = running_odometer;
    eeOdometer.trip_hundredths = running_trip;
    eeOdometer.count++;
    if (eeOdometer.count > EEPROM_WRITE_LIMT) {
      //Rotate address for Odometer
      eeOdometer.count = 0;
      eeConfig.odo_address += sizeof(eeOdometer);
      if (eeConfig.odo_address > EEPROM_SIZE) {
        eeConfig.odo_address = EEPROM_CONFIG_BUFFER;
      }
      EEPROM.put(eeAddress, eeConfig);
    }
    EEPROM.put(eeConfig.odo_address, eeOdometer);
  }
}

// callback for received data
void receiveData(int byteCount)
{
  // Maybe store a cmd to output requested data
  char cmd;
  while (Wire.available()) {
    cmd = Wire.read();
    if (cmd == 'T') {
      uint8_t s = SREG;
      cli();
      // Do Stuff
      running_trip = running_odometer;
      saveOdometer();
      SREG = s;
    }
  }
}

// callback for sending data
void sendData()
{
  Wire.write((const uint8_t *)&rpm, sizeof(rpm));
  Wire.write((const uint8_t *)&temp_oil, sizeof(temp_oil));
  Wire.write((const uint8_t *)&speed, sizeof(speed));
  Wire.write((const uint8_t *)&supply_voltage, sizeof(supply_voltage));
  Wire.write((const uint8_t *)&running_odometer, sizeof(running_odometer));
  Wire.write((const uint8_t *)&running_trip, sizeof(running_trip));
  Wire.write((const uint8_t *)&pres_oil, sizeof(pres_oil));
}

void setup()
{
  if (debug) {
    Serial.begin(9600); // start serial for output
    Serial.println("Ready!");
  }
  // Setup "constants" configurable
  readEEPROM();

  SleepyPi.enableWakeupAlarm(false); // 2019-04-25 suddenly made the sleepypi stop working
  SleepyPi.rtcInit(false);
  SleepyPi.enablePiPower(false);
  SleepyPi.enableExtPower(false);

  // initialize i2c as slave
  Wire.begin(SLAVE_ADDRESS);

  // define callbacks for i2c communication
  Wire.onReceive(receiveData);
  Wire.onRequest(sendData);

  // Setup pins
  pinMode(rpmPulsePin, INPUT_PULLUP); // Interrupt
  pinMode(wheelPulsePin, INPUT_PULLUP); // Interrupt
  pinMode(bikeOnPin, INPUT_PULLUP);
  while (CAN_OK != CAN.begin(CAN_500KBPS, MCP_12MHz)) {            // init can bus : baudrate = 500k
    delay(100);
    if (debug) {
      Serial.println("CAN Initialization failing!");
    }
  }

  CAN.mcpPinMode(MCP_RX0BF,MCP_PIN_OUT);
  CAN.mcpDigitalWrite(MCP_RX0BF,LOW);

  // PinChangeInterrupt can always be abbreviated with PCINT
  attachPCINT(digitalPinToPCINT(bikeOnPin), bikeOn, CHANGE);
  disablePCINT(digitalPinToPCINT(bikeOnPin));

  attachInterrupt(digitalPinToInterrupt(rpmPulsePin), rpmPulse, FALLING);//Initialize the intterrupt pin (Arduino digital pin 2);
  attachInterrupt(digitalPinToInterrupt(wheelPulsePin), wheelPulse, FALLING);//Initialize the intterrupt pin (Arduino digital pin 3);

}

void loop()
{
  static long int oil_Temp_rb[10] = {0};
  static long int oil_Temp_sum = 0;
  static int oil_Temp_rb_i = 0;

  bool pi_running = SleepyPi.checkPiStatus(50, false);
  bike_running = !digitalRead(bikeOnPin);
  float rpi_current = SleepyPi.rpiCurrent();

  if ( ready_to_save_odo ) {
    saveOdometer();
    ready_to_save_odo = false;
  }

  if (debug) {
    Serial.print("Current: ");
    Serial.print(rpi_current);
    Serial.print(" pi_running=");
    Serial.print(pi_running);
    Serial.print(" bike_on=");
    Serial.println(bike_running);
  }

  if (debug) {
    bike_running = true;
    pi_running = true;
  }

  while (pi_running == false && bike_running == false) {
    debug_out("Going to Sleep\r\n");
    saveOdometer();
    delay(500);
    SleepyPi.enablePiPower(false);
    SleepyPi.enableExtPower(false);
    enablePCINT(digitalPinToPCINT(bikeOnPin));
    CAN.mcpDigitalWrite(MCP_RX0BF,HIGH);
    SleepyPi.powerDown(SLEEP_FOREVER, ADC_OFF, BOD_OFF);
    disablePCINT(digitalPinToPCINT(bikeOnPin));
    CAN.mcpDigitalWrite(MCP_RX0BF,LOW);
    pi_running = SleepyPi.checkPiStatus(50, false);
    bike_running = !digitalRead(bikeOnPin);
  }


  if (bike_running) {
    time_BikeOff = 0;
    if (pi_running) {
      // Turn on power
      // Usually redundant, but keeps from resetting the Pi when turning off software power jumper
      SleepyPi.enablePiPower(true);
      SleepyPi.enableExtPower(true);
    } else {
      // Bike is on, but Pi is not, reset power to Pi
      // This handles a situation where Pi shutdown on its own
      SleepyPi.enablePiPower(true);
      SleepyPi.enableExtPower(true);
      debug_out("Wait 5s for pi to start running.\r\n");
      delay(5000);
      pi_running = SleepyPi.checkPiStatus(50, false);
      if (!pi_running) {
        debug_out("Turning off Pi.\r\n");
        SleepyPi.enablePiPower(false);
        SleepyPi.enableExtPower(false);
        delay(50);
        debug_out("Turning on Pi.\r\n");
        SleepyPi.enablePiPower(true);
        SleepyPi.enableExtPower(true);
      }
    }

  } else {
    if (time_BikeOff == 0) {
      time_BikeOff = time;
    }
    if (pi_running) {
      if (time - time_BikeOff > SHUTDOWN_DELAY) {
        SleepyPi.piShutdown(50); // argument is threshold mA to detect pi is shut off
        SleepyPi.enableExtPower(false);
        SleepyPi.enablePiPower(false);
      }
    }
  }
  time = millis();

  delay(10);  // voltage reading is artificially high if we don't delay first
  supply_voltage = SleepyPi.supplyVoltage();

  // Calculate RPM
  cli();
  wkgTime = RPM_interval;
  sei();
  if (micros() > ( rpm_time_last + MICROS_SECOND ) ) {
    wkgTime = MAX_UINT16_T;
    rpm = 0;
  }

  if (wkgTime < MAX_UINT16_T) {
    // ( s/min * us/s / us/C*pulse ) * C = RPM
    // RPM_CONV is constant to solve equation since only variable is pulse time
    rpm = (RPM_CONV / wkgTime);
  }

  // Calculate Speed (x100)
  cli();
  wkgTime = SPEED_interval;
  sei();
  if (micros() > ( speed_time_last + MICROS_SECOND ) ) {
    wkgTime = MAX_UINT16_T;
    speed = 0;
  }

  if (wkgTime < MAX_UINT16_T) {
    // MPH_CONV is a constant calculated to solve to equation, since the only variable is pulse time
    speed = ( MPH_CONV / wkgTime);
  }

  // Keep track of Oil Temp
  oil_Temp_rb_i++;
  if (oil_Temp_rb_i >= 10) {
    oil_Temp_rb_i = 0;
  }
  oil_Temp_sum -= oil_Temp_rb[oil_Temp_rb_i];
  oil_Temp_rb[oil_Temp_rb_i] = Thermistor(analogRead(oil_Temp_pin)) * 100;
  oil_Temp_sum += oil_Temp_rb[oil_Temp_rb_i];
  temp_oil = oil_Temp_sum / 10;


  // Store oil pressure
  delay(10); // allow ADC to settle
  pres_oil = oilPressure(analogRead(oil_pres_pin)) * 100;
  pres_oil = compensateOilPressure(pres_oil,temp_oil);

  if (debug) {
    delay(500);
    Serial.print("Speed Pulses:");
    Serial.print(speed_pulse_count, DEC);
    Serial.print(" SPEED: ");
    Serial.println(speed, DEC);
    Serial.print("RPM Pulses:");
    Serial.print(rpm_pulse_count, DEC);
    Serial.print(" RPM: ");
    Serial.println(rpm, DEC);
  }

  while (CAN.checkReceive() == CAN_MSGAVAIL) {
    static unsigned long CanId = 0;
    byte CanLen;
    byte CanBuf[8];
    byte canReadRet = CAN.readMsgBuf(&CanLen, (byte *)&CanBuf);
    CanId = CAN.getCanId();
    if ( CanId == CANID_RESET_TRIP  && CanBuf[0] == 0xFF) {
      uint8_t s = SREG;
      cli();
      // Do Stuff
      running_trip = running_odometer;
      saveOdometer();
      SREG = s;
    }
  }
  static unsigned long last_engine1 = 0;
  if ( last_engine1 + CAN_ENGINE1_RATE < millis()) {
    byte _response[8] = {0};
    _response[0] = rpm;
    _response[1] = rpm >> 8;
    uint8_t _speed = speed / 100;
    _response[2] = _speed;
    uint8_t _pres = pres_oil / 100;
    _response[3] = _pres;
    uint16_t _temp = (temp_oil / 100) + 50;
    _response[4] = _temp;
    _response[5] = _temp >> 8;
    uint8_t _volts = supply_voltage * 10.0;
    _response[6] = _volts;
    CAN.sendMsgBuf(CANID_ENGINE1, 0, 7, _response);
    last_engine1 = millis();
  }
  static unsigned long last_engine2 = 0;
  if ( last_engine2 + CAN_ENGINE2_RATE < millis()) {
    byte _response[8] = {0};
    uint32_t _trip = (running_odometer - running_trip) * 1.609344 / 10.0;
    uint32_t _odo = running_odometer * 1.609344 / 10.0;
    _response[0] = _odo;
    _response[1] = _odo >> 8;
    _response[2] = _odo >> 16;
    _response[3] = _trip;
    _response[4] = _trip >> 8;
    _response[5] = _trip >> 16;
    CAN.sendMsgBuf(CANID_ENGINE2, 0, 6, _response);
    last_engine2 = millis();
  }
}

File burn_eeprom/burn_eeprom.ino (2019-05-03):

#include <EEPROM.h>
#include "../EDL_eeprom.h"

void setup() {
	config mConfig;
	EEPROM.get(0,mConfig);
	//mConfig.odo_address = 128;
	//mConfig.rear_teeth = 42;
	mConfig.rear_diameter = 2500; //2621
	//mConfig.shutdown_delay = 300000;
	EEPROM.put(0,mConfig);

	odometer mOdo;
	EEPROM.get(mConfig.odo_address,mOdo);
        //mOdo.miles_hundredths = 5924201;
        mOdo.trip_hundredths = 5911358;
	EEPROM.put(mConfig.odo_address,mOdo);
}

void loop() {
	// Empty Loop
}

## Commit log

2019-03-27 Added initial code to monitor oil temperature, should get moved to its own file.
2019-04-21 Updated constants for Thermistor
2019-04-23 Odometer value read from EEPROM and incremented based off wheel diameter, also stored in EEPROM
2019-05-04 Added ability to reset trip via I2C command
    [engine_data.ino]
2020-03-29 Added support for oil pressure
2023-06-30 New hardware adjustments
    Changed pin numbers. Moved vsw to pin 9, and clarified A0 and A1 instead of 14,15
    Added save odometer every mile.
    Modified conversion for pressure.
2024-02-24 Add hardware files
    [5V-LMR33630.kicad_sch, BOM-EngineData.csv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]
2024-04-13 edit pressure calc
2025-04-24 Changed oil pressure to absolute. Maybe
2025-04-25 Fix, regression oil temp variable size
    [engine_data.ino]
2025-05-15 Rudimentary compensation of oil pressure with temp.
